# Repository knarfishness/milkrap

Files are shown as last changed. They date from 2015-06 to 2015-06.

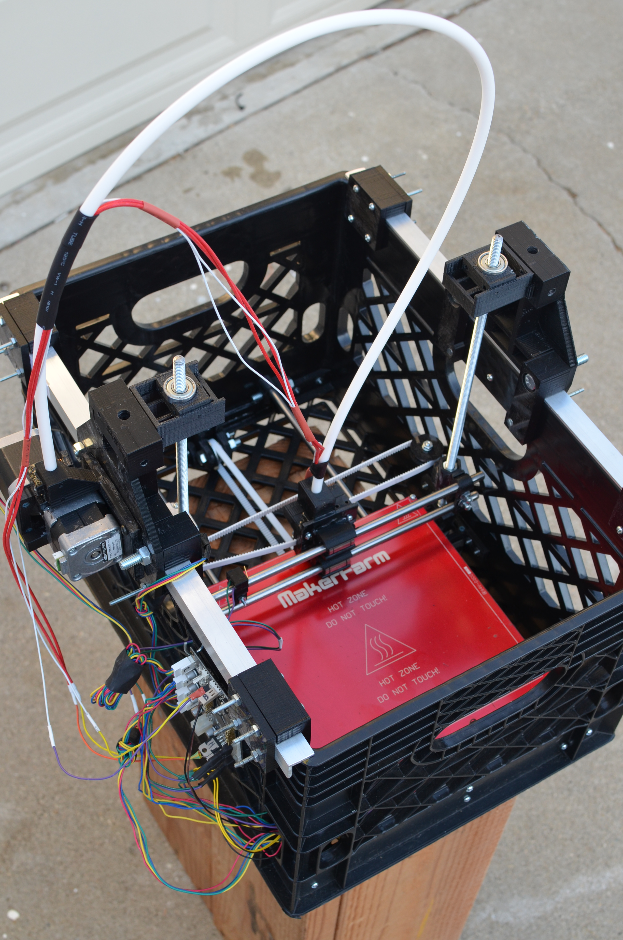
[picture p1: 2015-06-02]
Photos/DSC_0165.JPG

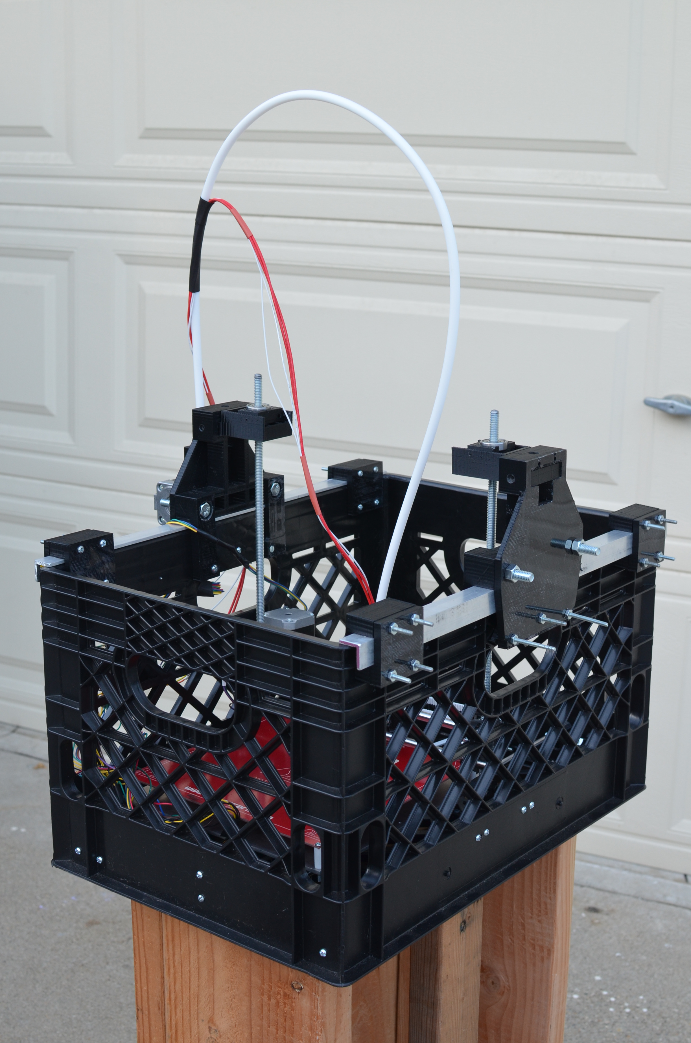
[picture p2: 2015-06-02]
Photos/DSC_0205.JPG

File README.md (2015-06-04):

# MilkRap
Organized version of the files for the MilkRap RepRap 3D printer detailed here:

[Original Instructable](http://www.instructables.com/id/MilkRap-Milk-Crate-RepRap/)

Full credit for design goes to the original author, gmdownes: http://www.instructables.com/member/gmdownes/

Files have been divided into STL (for printing) and SKP (for editing in SketchUp). I have also included the original pictures and generated gCode files, although if you're printing, you'll want to be creating your own from the STL files.

#Table of Contents
1. [Step 1: Background](#step1)
2. [Step 2: Advantages over a RepRap Prusa Mendel V2](#step2)
3. [Step 3: Download and print the STL or SKP files for the plastic parts](#step3)
4. [Step 4: Use the jigs](#step4)
5. [Step 5: Standard RepRap stuff](#step5)
6. [Step 6: Milk Crate reinforcement](#step6)
7. [Step 7: Z axis towers](#step7)
8. [Step 8: Bowden / Direct Drive Extruder](#step8)
9. [Step 9:  Thats It !!](#step9)

# Build of Materials
| Part | Link | Quantity  |
| --- |:---:| -----:|
| Milk Crate | http://milkcratesdirect.com | 1 |
| Z Nut Holder | https://github.com/knarfishness/milkrap/blob/master/STL/Z_Nut_Holder.stl | 2 |
| Y Axis Bearing Holder | https://github.com/knarfishness/milkrap/blob/master/STL/YaxisBearingTower_fixed.stl | 1 |

# Reorganized README
Image Title

This instructable describes how and why I made a RepRap Prusa Mendel V2 integrated into a Milk Crate (Dairy Crate).

Image Title

<div id='step1'/>
## Step 1: Background

I have been a Maker in the purest form since I was a kid, and I am so glad that there is now a name (and community and movement) for what I am. Just a few years ago I would have to refer to myself as a "guy who liked to take things apart to see how they worked and also build stuff". Just saying "I'm a Maker" is sooo much easier. 

I purchased a RepRap Prusa Mendel V2 kit from the good folks at Maker Farm (thank you Colin for all your support) about 8 months ago and immediately fell in love with the machine and with 3-D printing.  But a few things about the Prusa struck me as opportunities for improvement. In particular was that to build a Prusa, the first thing to do is make a frame out of thin air (not literally of course, but constructing the frame from threaded rods is a slow process requiring lots of measuring, cutting, joining, leveling, and plumbing). So I began thinking of ways to build a Prusa into a rigid frame that was easy to construct (good) or already constructed (better). 

I am also an avid fan of recycling and finding alternative uses for objects borrowed from other industries. Then, I either saw or remembered seeing piles of milk crates sitting behind a convenience store getting dirty and abused, or milk crates being used as shelving in a college dorm, or as a  step stool in a mechanics garage, etc. It struck me that milk crates are everywhere you look and are also built to be very strong. As it turns out, the interior dimensions of a rectangular milk crate is big enough to insert the working parts of a Prusa Mendel and achieve the same build area in the X and Y direction and...

<div id='step2'/>
## Step 2: Advantages over a RepRap Prusa Mendel V2

Image Title

get even more buildable area in the Z direction!

Because the rigidity of the milk crate comes from the sides and base, it doesn't need upper crossing members for support (as the Prusa does). This allows the X carriage to move and print as high as your imagination (provided you use Z axis threaded rods long enough and create support towers (see step 10) large enough to hold them. A  standard Prusa that comes with a Greg's Accessible Extruder like the one I ordered has an actual print area of about X=7.5" before the extruder motor hits the Z axis threaded rod, Y=8.5", and Z=4.5" before the large extruder gear hits the upper threaded rod crossing member. That is an actual build area of about 287 cubic inches. 

Changing the extruder to a smaller Bowden tube style would capture another inch in the X direction and almost 3" in the Z direction so the print area increases to 542 cubic inches but there is still an eventual limit in the Z direction due to the crossing members. 

Other advantages of the MilkRap design are: 

1. Easier to build for a novice or non-technical person
2. Much faster to build
3. Extremely portable
4. Very durable
5. Milk crates are cheap (please remember that taking a milk crate from behind a store, etc is stealing. I purchased my milk crate from http://www.milkcratesdirect.com/ for $8 plus shipping
6. Milk crates provide lots of places to attach unruly wires
7. All belts are tension-able in place using tensioning screws
8. Lighter/minimalist X and Z carriages to reduce weight and increase speed
9. Simplified custom Bowden Tube / Direct Drive extruder
10. Z axis threaded rods are easily plumbed
11. No more bulky 5/16" bolts in the Y and X idlers
12. A great conversation starter!

<div id='step3'/>
## Step 3: Download and print the STL or SKP files for the plastic parts

Image Title

Files are HERE!!

[Original Dropbox Files](www.dropbox.com/sh/37b4i8u9jlcf2ct/Q4O8GUcQ5J)

You can also use the `Download as ZIP` option from GitHub's side menu for the reorganized version included with this repo.

See comments for extra notes.

<div id='step4'/>
## Step 4: Use the jigs

Image Title
Image Title
Image Title
Image Title
Image Title
Image Title
Image Title

1. Use the printed jigs to position and drill attachment holes for the Y axis smooth rod, motor, and idler mounts as well as the Z axis motor mounts. The jigs are designed to be a negative match of the physical geometry of the milk crate and ensure exact placement of mounting holes. 
2. Slide linear bearings over Y axis smooth rods and Insert rods into rod mounts. 
3. Attach mounts to the milk crate via holes from previous step with 6-32 screws and nuts. 
4. Attach Y motor to motor mount and motor mount to milk crate. 
5. Now attach Y idler to milk crate the same way. The Y idler uses a standard 608 skate bearing. Lots of Prusa kits come with 5/16 bolts to attach these bearings. To me that was like using a sledge hammer as a fly swatter so I printed some 5/16" OD 9/64"ID inserts to be able to attach the bearings with 6-32 machine screws. I used the same inserts to attach the 608 bearing in the X idler. Attach Z axis motors to mounts and mounts to milk crate via holes drilled previously.

<div id='step5'/>
## Step 5: Standard RepRap stuff

Image Title
Image Title
Image Title
Image Title

Because this is a RepRap based printer, a lot of the build procedures are very similar to building a RepRap. So, to save time I will refer you to the myriad online sources of instructions for building a RepRap including (https://docs.google.com/file/d/0B80A_woXoRWdYmZFeFBkR3NvOXM/edit and http://reprap.org/wiki/RepRap_Options) These web pages will guide you through the basic processes used in building these parts of your Milk Strap: Y axis smooth rods to linear bearings and build plate (heated or not), X axis motor mount and idler attachment to X axis smooth rods and Z axis threaded rods, attaching all wires and electronic components.

<div id='step6'/>
## Step 6: Milk Crate reinforcement

Image Title
Image Title
Image Title
Image Title
Image Title
Image Title
Image Title
Image Title
Image Title
Image Title
Image Title

Although milk crates are designed to be very tough, I did find it necessary to add a piece of 3/4" x 3/4" x 1/8" thick aluminum angle to the long edges at the top of the crate. I chose to mount the aluminum in a way that did not require drilling through it (though in hind sight that may have been easier or at least used smaller/fewer printed parts. The jigs used to position the mounting holes remain in place after the holes are drilled and become a permanent part of the machine. Jigs are placed and holes drilled for the two outside brackets and one middle bracket. Aluminum is manually held in place while the other parts of the brackets are bolted on. Now the aluminum is secure. The middle bracket is much larger than the outer brackets and becomes the Z axis tower. This tower holds the tops of the Z axis threaded rods in place.

<div id='step7'/>
## Step 7: Z axis towers

Image Title
Image Title
Image Title
Image Title
Image Title
Image Title

The Z axis towers are the key to the "unlimited" Z axis printing height of this machine. Because this is the first iteration of this machine I have produced, I chose a Z tower height I was absolutely sure would be stable while the machine was printing. I highly encourage you to manipulate the SKP files to create larger/higher towers and push the envelope, just make sure the wall thicknesses and geometry of the towers can support the height you choose. I will be doing the same when I get a chance. I hope to hear from you! The towers are topped with a two piece system. The first piece is inserted into the main body of the tower and is designed as a "track" in which the second piece (which holds the bearing) can slide in either direction along the X axis. Using a plumb bob, the bearing holder is positioned by the builder until the 5/16" Z axis threaded rod is plumb. Once plumb is attained, the bearing holder is permanently affixed to the track via small screws.

<div id='step8'/>
## Step 8: Bowden / Direct Drive Extruder

Image Title
Image Title
Image Title
Image Title
Image Title

Image Title
Image Title
Image Title

I chose to use a Bowden tube extruder with a direct drive feed system as this spoke to my desire for simplicity. Neither of these pieces are ground breaking on their own and many versions of these devices can be found on the web. I chose to use a Mk-2 J-head hot end because it is the same one that came with my Maker Farm Prusa and it has worked without flaw. The PTFE Bowden tube is held in place via a simple holder and sharp set screws that pierce the PTFE Bowden tube but do not penetrate all the way through (drywall screws work well but are a bit big, or you can sharpen a small #2 wood screw). The extruder is my own design. I had read some opinions that a NEMA 17 does not have enough torque to direct drive 3mm filament so I figured I would hedge my design by using two NEMA 17's rotating in opposite directions (each with a MK-7 drive gear). 

<div id='step9'/>
## Step 9: Thats It !!

MilkRap Creator

Milk Raps really are easy to build, especially compared to a Prusa V2. I see that the Prusa i3 addresses many of the issues I had with the Prusa V2, and although I have not seen an i3 up close, it doesn't appear to have the durability or portability of a Milk Rap and it still has a crossing member that will ultimately define the Z axis max height. Really though, at the end of the day I just had to make my own machine. Makers gotta make and hackers gotta hack (the good kind).

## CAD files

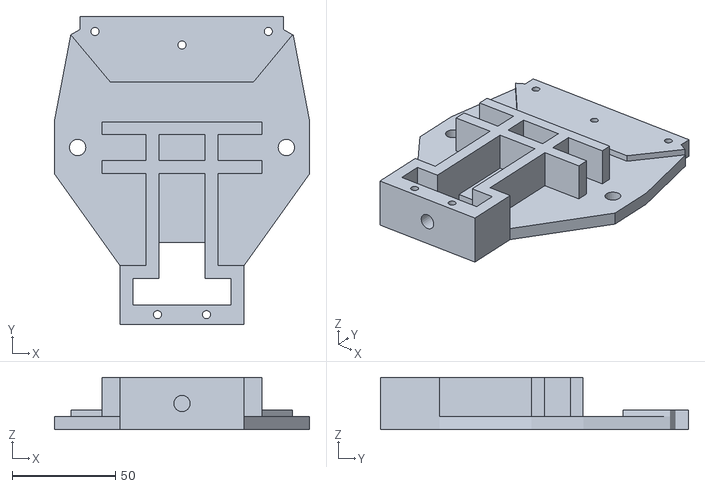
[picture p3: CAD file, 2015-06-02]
STL/Z_Tower_Main_Body.stl
123.7 x 149.2 x 25.4

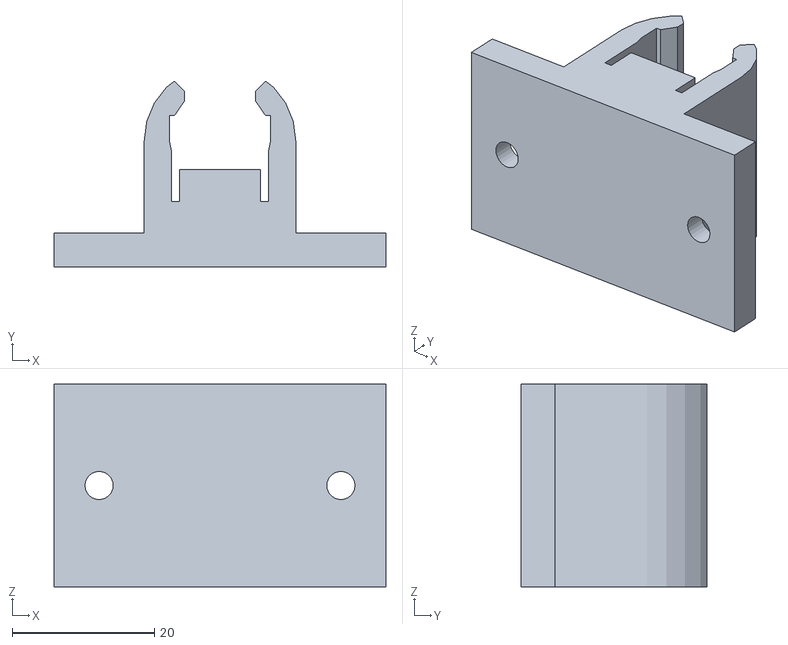
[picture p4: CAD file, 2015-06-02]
STL/LM8UU Linear Bearing Holder_w_Tabs.stl
46.8 x 26.2 x 28.6

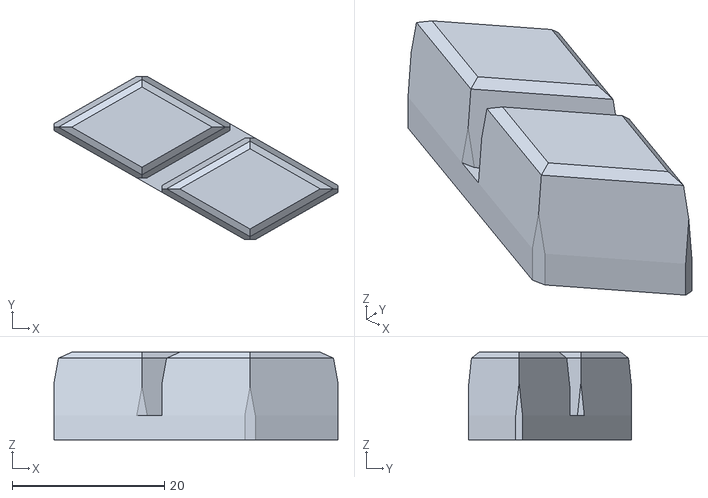
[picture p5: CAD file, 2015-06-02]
STL/Test Trapazoids/Test_Trapazoid_5_x_2.stl
37.3 x 21.4 x 11.5

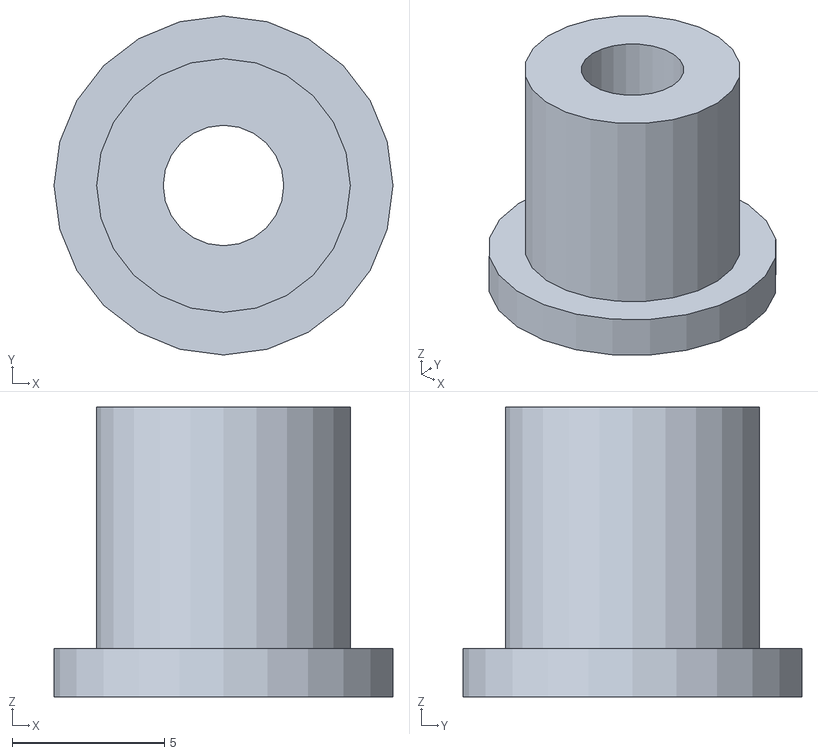
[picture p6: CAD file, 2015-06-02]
STL/Bearing_Sleeve_Inner_4.stl
11.1 x 11.1 x 9.53

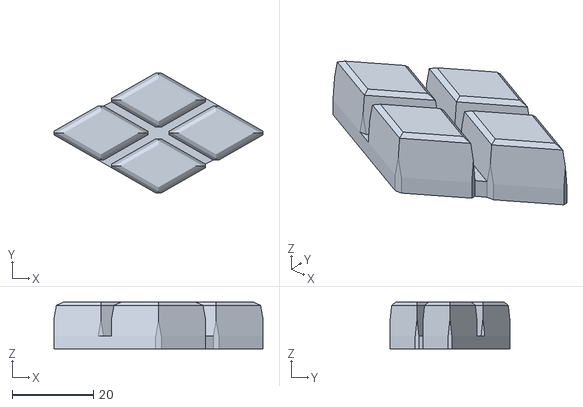
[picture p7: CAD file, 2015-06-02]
STL/Test Trapazoids/Test_Trapazoid_5_x_4.stl
51.5 x 29.6 x 11.5

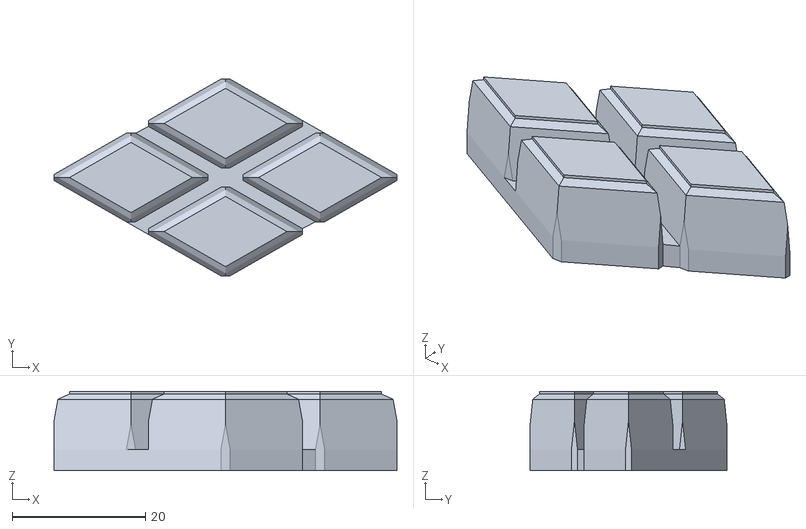
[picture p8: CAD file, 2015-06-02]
STL/Test Trapazoids/Test_Trapazoid_6_x_4.stl
51.5 x 29.6 x 11.9

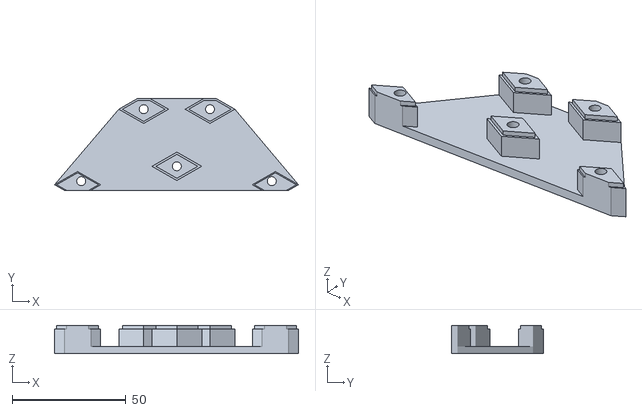
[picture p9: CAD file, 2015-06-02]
STL/Z-towerBaseTraps_3.stl
107.4 x 40.4 x 12.3

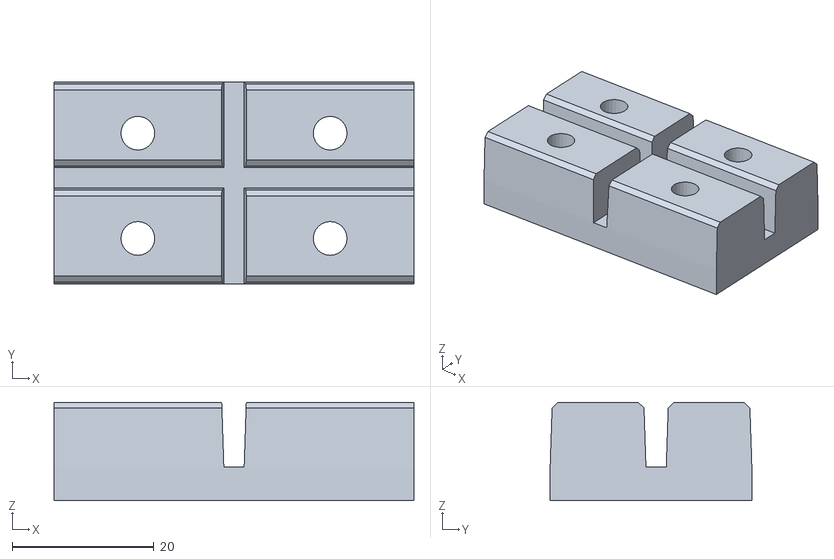
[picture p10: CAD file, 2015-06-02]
STL/Alum_Rail_Outer_Base.stl
50.8 x 28.5 x 13.9

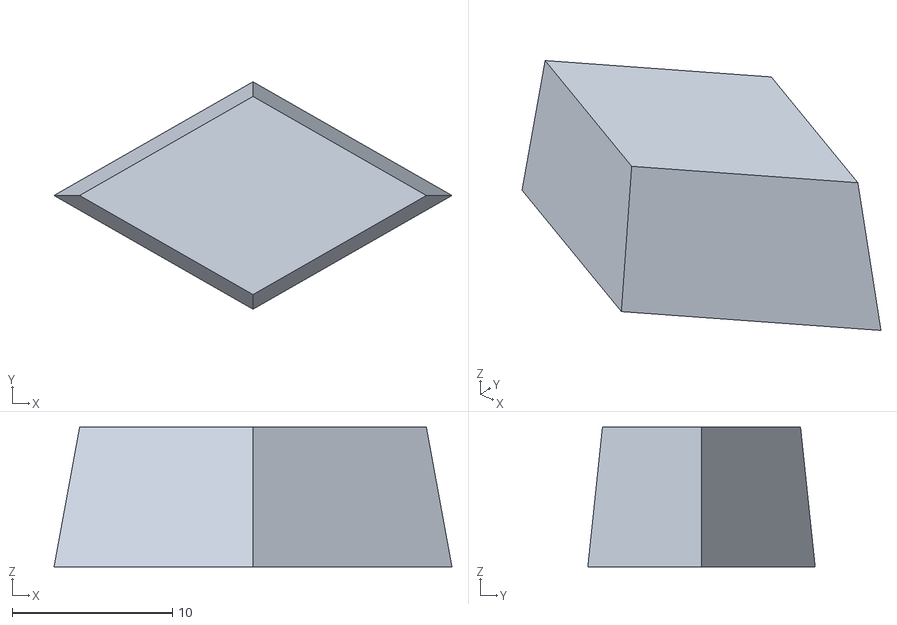
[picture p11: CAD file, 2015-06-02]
STL/Test Trapazoids/Test_Trapazoid_4.stl
24.8 x 14.2 x 8.73

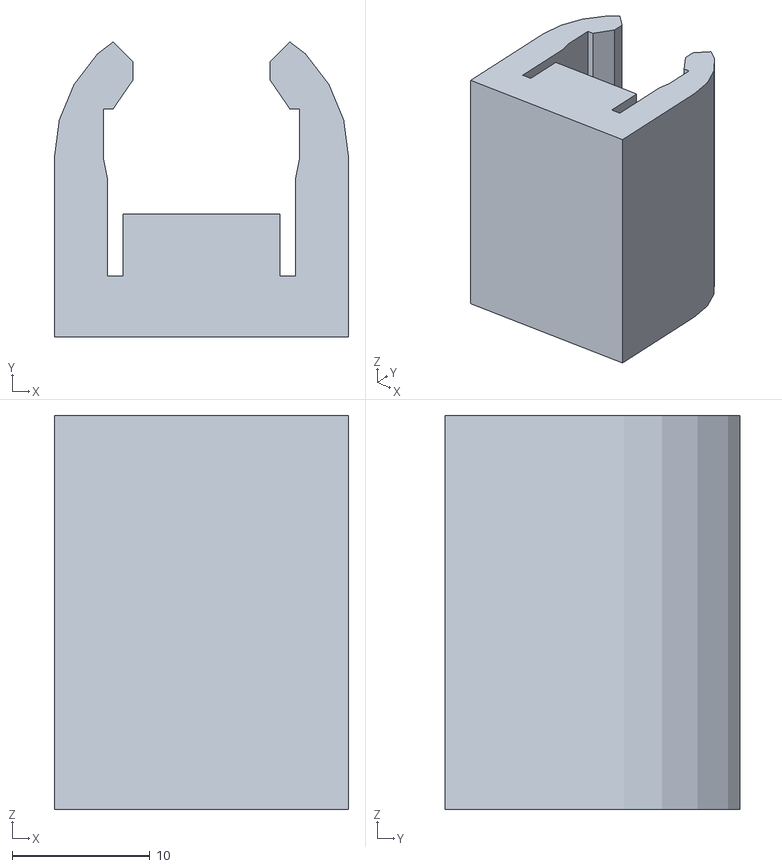
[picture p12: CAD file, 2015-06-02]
STL/LM8UU Linear Bearing Holder.stl
21.4 x 21.4 x 28.6

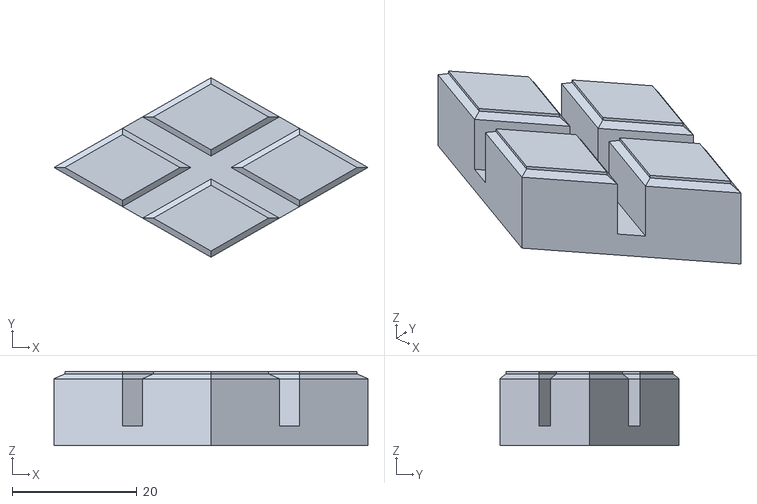
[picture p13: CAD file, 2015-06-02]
STL/Test Trapazoids/Test_Trapazoid_7_x_4.stl
50.3 x 28.8 x 11.9

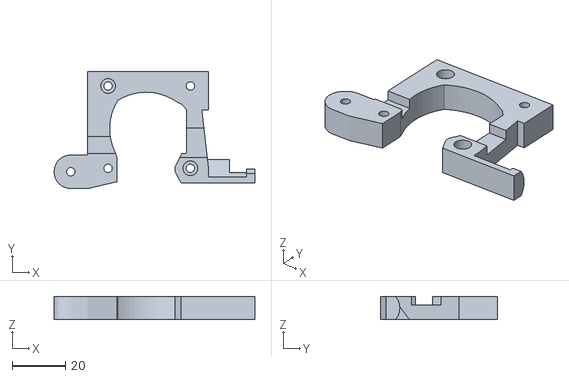
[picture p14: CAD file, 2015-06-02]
STL/Extruder Pivot.stl
75.7 x 44.2 x 8.73

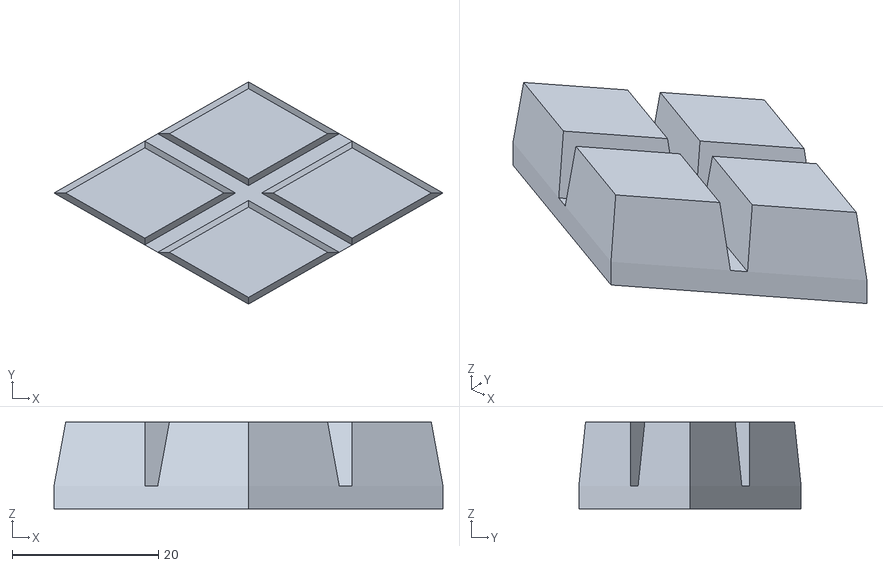
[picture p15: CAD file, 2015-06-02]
STL/Test Trapazoids/Test_Trapazoid_4_x_4_2.stl
53.2 x 30.4 x 11.9

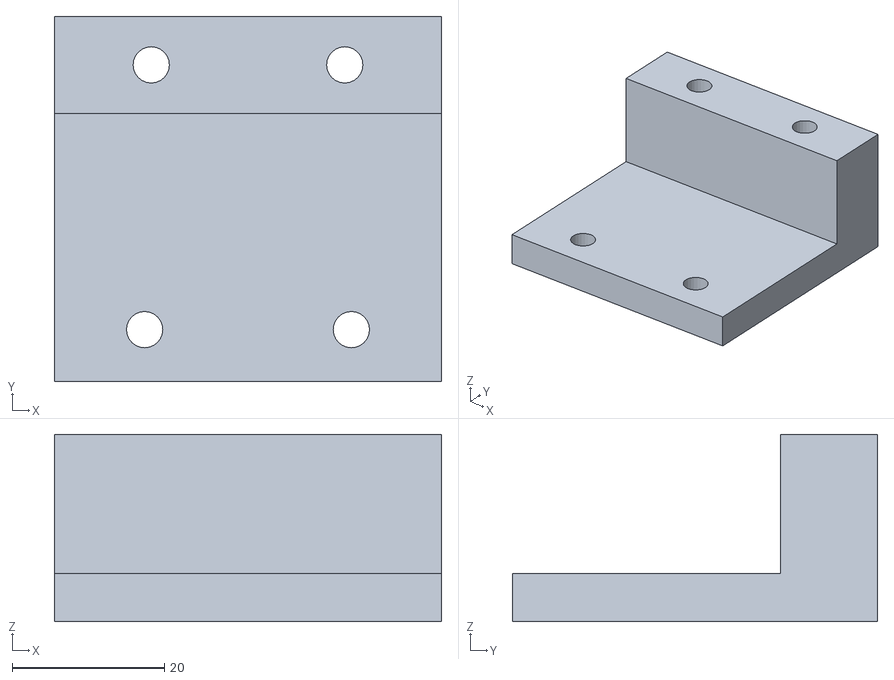
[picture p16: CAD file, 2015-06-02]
STL/Alum_Rail_Inner.stl
50.8 x 47.9 x 24.6

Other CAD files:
STL/Test Trapazoids/Test_Trapazoid_2.stl
STL/Test Trapazoids/Test_Trapazoid.stl
STL/Z_actual Bearing Mount No Really.stl
STL/Rod to Motor Clamp_2.stl
SKP/JIG_Z_Motor_Mounts_Hole_Spacing_Fixed_6-4-13.skp
SKP/Milk Strap A_1_a.skp
SKP/Milk Strap B_1_a.skp
SKP/NEW_X-Z_motor.skp
SKP/Prusa Mendel V2 - X End Motor.skp
SKP/Z_Carriages.skp
SKP/Z_Carriages_6_11_13.skp
STL/5_16x1 inch x 3_16 thick washer.stl
STL/Alum_Rail_Outer.stl
STL/BIG_bearing filler.stl
STL/BIG_washer.stl
STL/Bearing_Sleeve_Inner.stl
STL/Bearing_Sleeve_Inner_2.stl
STL/Bearing_Sleeve_Inner_3.stl
STL/Bearing_Sleeve_Inner_5.stl
STL/Bowden Clamp.stl
STL/Bowden Extruder Top.stl
STL/EndStop Switch Holder.stl
STL/Extruder Stationary.stl
STL/JIG_Y Belt Tensioner.stl
STL/JIG_Y axis Rod Holder.stl
STL/JIG_Z_Motor_Mount.stl
STL/Nubbin_Belt base.stl
STL/Nubbin_Belt top ribbed _Xtra Crazy.stl
STL/Nubbin_Belt top ribbed.stl
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

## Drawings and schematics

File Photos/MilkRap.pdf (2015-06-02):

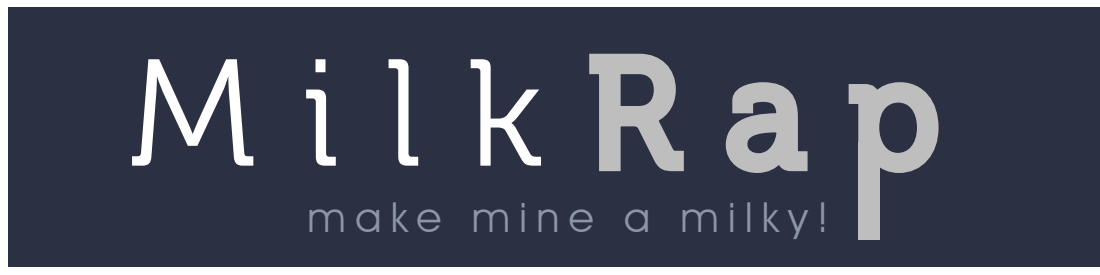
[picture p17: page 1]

make mine a milky!
